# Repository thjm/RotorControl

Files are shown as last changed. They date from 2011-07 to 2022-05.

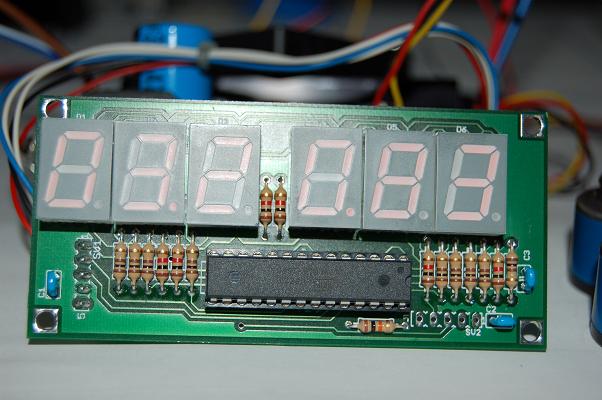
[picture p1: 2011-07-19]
DisplayUR/Doc/Display.jpg

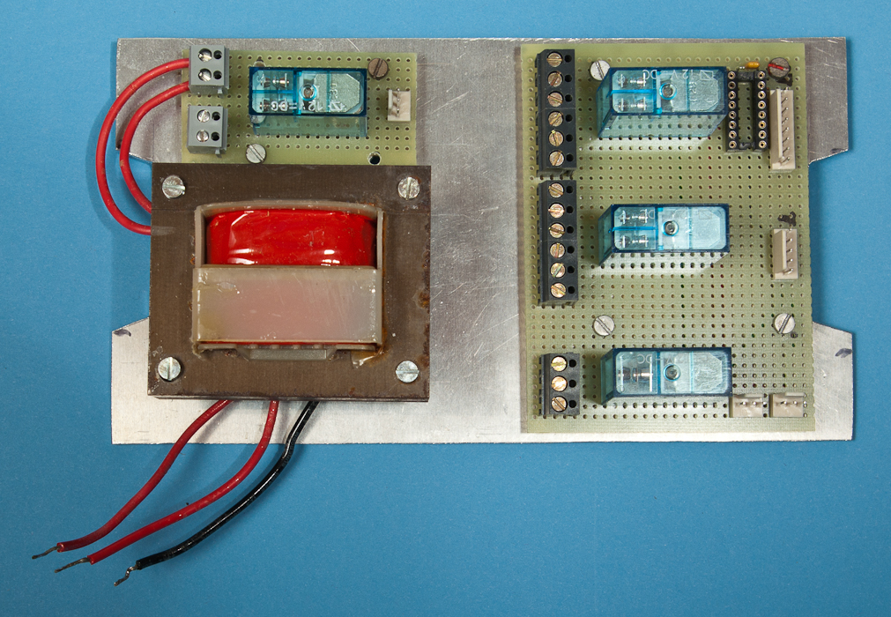
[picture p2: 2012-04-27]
Docu/RelayMountingPlate.jpg

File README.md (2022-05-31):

# About

RotorController is for controlling a simple antenna rotator using directionaly
signals from a 3D magnet sensor (and from a 3D accelerometer).

The software is split onto several micro controllers from Atmel's AVR family.

- the software for the display board (hardware design based on ATmega8 from U.Radig)
  is located in the directory ./DisplayUR
- the software for the ATmega8 at the remote magnetic/accelerometric sensor is
  located in the directory ./LSM303
- the software foreseen to run on the main ATmega32 is in the ./ directory
- further we have the Eagle circuit drawing of the various boards (my boards are
  all done on prototype boards, thus the eagle design was never verified):
  - AntennaBoard.sch : board with the mag./acc. sensor attached
    to the boom of the antenna
  - ButtonBoard.sch : board to hold push buttons and LEDs for the front panel
  - CPUBoard.sch : the board with the main CPU and connectors to the other
    board with a micro controller on them
  - PowerSupply.sch : main power supply, +12V and +5V
  - RelayBoard1.sch : board which holds relays for the direction and the release
    of the rotor brake (if available)
  - RelayBoard2.sch : supplement relay board, switches extra 22V AC for the
    used rotor type

## Directories

- Bootloader : contains the boot loader for the antenna sensor uC (not yet used?)

- Docu : various documentation files

- DisplayUR : parts takes from Ulrich Radig's (http://www.ulrichradig.de)
          PowerSupply project. The display unit presented there seems to be
          quite usable for a simple display here, just software needs to be
          adopted.

- Eagle : contains drawings and schemes done with the Eagle layout program

- Linux : various test programs, to be run on Linux

- LSM303 : library and example for the Pololu LSM303DLH 6-axis sensor
          breakout board. The boards contains a 3-axis magnetometer and a
          3-axis accelerometer.
          See also:
  - http://www.lipoly.de/index.php?main_page=product_info&products_id=165628
  - data sheet LSM303DLH.pdf
  - LSM303DLH-compass-app-note.pdf
  - LSM303DLH-orangutan-example-cde.zip
  - UM10204.pdf (I2C-bus specification)
  - https://github.com/ryantm/LSM303DLH (Arduino library)

- Sketches : Arduino sketches collection

- Test : directory containing various test programs for the 'rotorcontrol'
         hardware environment

## Requirements

- you need a cross-build environment for AVR micro controllers.
- the UART library from Peter Fleury, unpacked to a local directory
- the TWI master library from Peter Fleury, unpacked to a local directory
- the environment variable FLEURYHOME must point to the root of both directories

## Usage

Compile the software in the 3 directories ./LSM303, ./DIsplayUR and ./ by
typing make in ./ We have then:

- ./LSM303/lsm303read.hex : the software for the mag./acc. controller
- ./DisplayUR/i2cdisplay.hex : the software for the I2C controlled LED display
- ./rotorcontrol.hex : the software for the main processor

## Project Details

### Revision 1.1

- the display of UR's PS1 project will be used to display the current and the
  set value for the azimuth (directory DisplayUR)

- a LSM303DLH accelerometer and compass module will be used to determine the
  antenna direction. It will be coupled to the main electronics via a serial
  interface (coupled via RS-485)

- the main electronics module has the task to
  - receive direction information from the LSM303DLH
  - calculate/average the direction information and send it to the display
    module
  - compare the current direction with the preset value and pass this
    information to the rotator controller (software module)
  - switch the rotator motor in an appropriate way to achieve the desired
    direction; handle (optional) end-switches and a clutch/brake
  - get users input via push buttons (attached to the main electronics or to
    the display module?)
  - ...

### Revision 2.x

Managed somehow to destroy the antenna sensor during comissioning. As sensor is no
longer available, purchased successor LSM303DLHC (GY-511).

## References

- http://homepage.hispeed.ch/peterfleury/doxygen/avr-gcc-libraries/group__pfleury__uart.html, UART library
- http://homepage.hispeed.ch/peterfleury/doxygen/avr-gcc-libraries/group__pfleury__ic2master.html, TWI library
- https://github.com/ryantm/LSM303DLH, Arduini library for LSM303 like sensors

- https://pre-commit.com/

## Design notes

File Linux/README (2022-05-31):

$Id: README,v 1.2 2012/06/06 16:07:17 mathes Exp $

README file for Projekte/RotorControl/Linux
-----------------------------------------------------------------------------

This is the README file for the Linux (host) based test software (algorithms,
verification, etc.) of the rotator controller project.

analyzedat.cc - reads a file containing logged NMEA strings ($ACRAW sentences)
           acquired by the lsm303read.c program. The data are analyzed in two
	   passes:

	   1st pass: minimum and maximum values are determined
	   2nd pass: the magnetic (3D) heading of the acquired data is
	             calculated

	   The 3D heading is calculated using the MAG and ACC sensor readings.

compass1.cc - interactive version of the above program. This programs reads
           the NMEA strings from a serial interface which has to be specified
	   at the command line.

	   Different operation modes are possible:
	   c - calibration = acquiring data for new MAG min/max values
	   m - measure
	   d - debug output

*.dat - various data files from online

=============================================================================

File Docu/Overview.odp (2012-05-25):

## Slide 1

Relay 1

Rotator

2*22V

220V AC

Relay 4

Relay 2

@ antenna

LSM303

ATmega8

Relay 3

ULN2003

MAX485

220V AC

220V AC

12V-/5V-

0 0 0 1 2 3

MAX485

ATmega32

Buttons (5)

& LEDS (4)

MAX232

RS-232

Revision 1.1

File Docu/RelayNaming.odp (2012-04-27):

## Relay boards: naming scheme

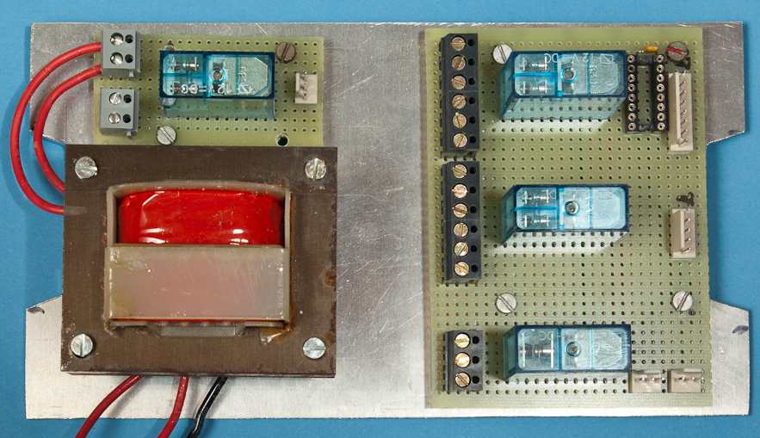
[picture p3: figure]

P1

S1

P1

S1

Relay K1

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
Relay K2

S2

O2

O1

S1

Relay K3

P1

## Relay boards: cabling scheme

P1

S1

P1

S1

Relay K1

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
Relay K2

S2

O2

O1

S1

Relay K3

P1

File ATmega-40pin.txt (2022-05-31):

$Id: ATmega-40pin.txt,v 1.1 2012/04/11 21:29:31 mathes Exp $

Pinouts for 40 pin ATmega uController
------------------------------------------------------------------------------

       16/32             644                  644A/644PA/1284/1284P
---------------------------------------------------------------------
  1  PB0 (XCK/T0)       (PCINT8/XCK0/T0)      (PCINT8/XCK0/T0)
  2  PB1 (T1)           (PCINT9/CLK0/T1)      (PCINT9/CLK0/T1)
  3  PB2 (INT2/AIN0)    (PCINT10/INT2/AIN0)   (PCINT10/INT2/AIN0)
  4  PB3 (OC0/AIN1)     (PCINT11/OC0A/AIN1)   (PCINT11/OC0A/AIN1)
  5  PB4 (!SS)          (PCINT12/OC0B/!SS)    (PCINT12/OC0B/!SS)
  6  PB5 (MOSI)         (PCINT13/MOSI)        (PCINT13/MOSI)
  7  PB6 (MISO)         (PCINT14/MISO)        (PCINT14/MISO)
  8  PB7 (SCK)          (PCINT15/SCK)         (PCINT15/SCK)
  9  !RESET
 10  VCC

 11  GND
 12  XTAL2
 13  XTAL1
 14  PD0 (RXD)          (PCINT24/RXD0)        (PCINT24/RXD0)
 15  PD1 (TXD)          (PCINT25/TXD0)        (PCINT25/TXD0)
 16  PD2 (INT0)         (PCINT26/INT0)        (PCINT26/RXD1/INT0)
 17  PD3 (INT1)         (PCINT27/INT1)        (PCINT27/TXD1/INT1)
 18  PD4 (OC1B)         (PCINT28/OC1B)        (PCINT28/XCK1/OC1B)
 19  PD5 (OC1A)         (PCINT29/OC1A)        (PCINT29/OC1A)
 20  PD6 (ICP1)         (PCINT30/OC2B/ICP1)   (PCINT30/OC2B/ICP1)

 21  PD7 (OC2)          (PCINT31/OC2A)
 22  PC0 (SCL)          (PCINT16/SCL)         (PCINT16/SCL)
 23  PC1 (SDA)          (PCINT17/SDA)         (PCINT17/SDA)
 24  PC2 (TCK)          (PCINT18/TCK)         (PCINT18/TCK)
 25  PC3 (TMS)          (PCINT19/TMS)         (PCINT19/TMS)
 26  PC4 (TDO)          (PCINT20/TDO)         (PCINT20/TDO)
 27  PC5 (TDI)          (PCINT21/TDI)         (PCINT21/TDI)
 28  PC6 (TOSC1)        (PCINT22/TOSC1)       (PCINT22/TOSC1)
 29  PC7 (TOSC2)        (PCINT23/TOSC2)       (PCINT23/TOSC2)
 30  AVCC

 31  GND
 32  AREF
 33  PA7 (ADC7)         (PCINT7/ADC7)         (PCINT7/ADC7)
 34  PA6 (ADC6)         (PCINT6/ADC6)         (PCINT6/ADC6)
 35  PA5 (ADC5)         (PCINT5/ADC5)         (PCINT5/ADC5)
 36  PA4 (ADC4)         (PCINT4/ADC4)         (PCINT4/ADC4)
 37  PA3 (ADC3)         (PCINT3/ADC3)         (PCINT3/ADC3)
 38  PA2 (ADC2)         (PCINT2/ADC2)         (PCINT2/ADC2)
 39  PA1 (ADC1)         (PCINT1/ADC1)         (PCINT1/ADC1)
 40  PA0 (ADC0)         (PCINT0/ADC0)         (PCINT0/ADC0)
==============================================================================

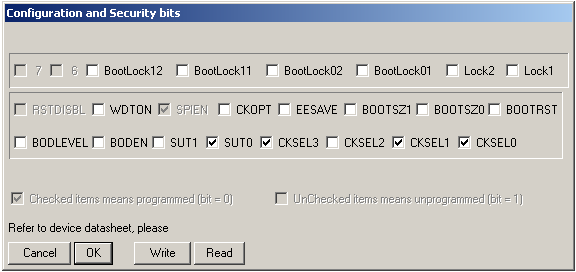
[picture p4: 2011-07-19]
DisplayUR/Doc/ATmega8_FuseBits.png

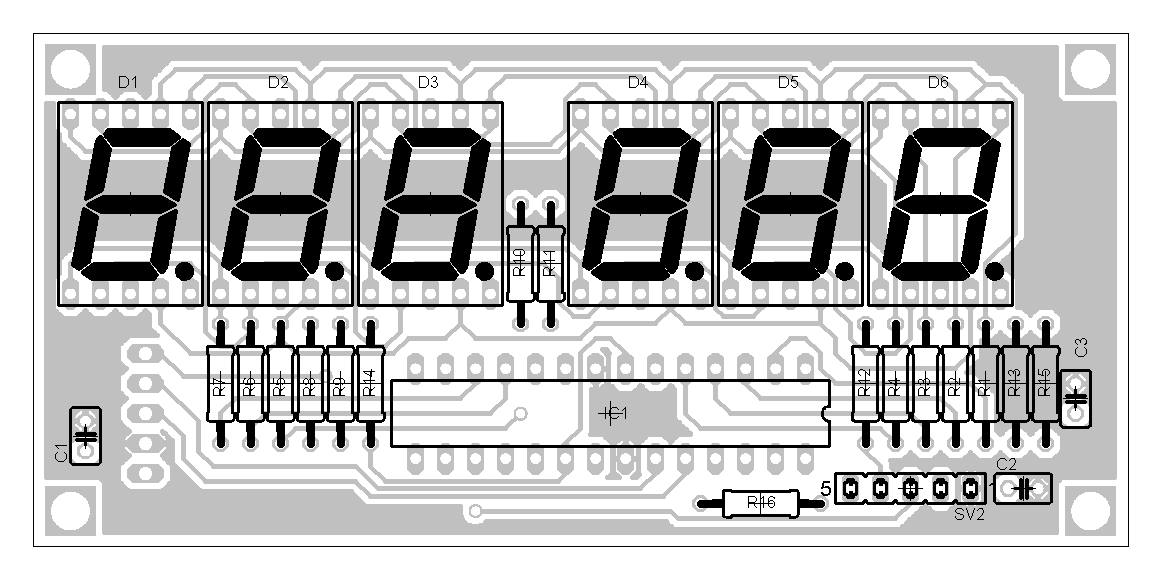
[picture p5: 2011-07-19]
DisplayUR/Doc/Display_Top.png

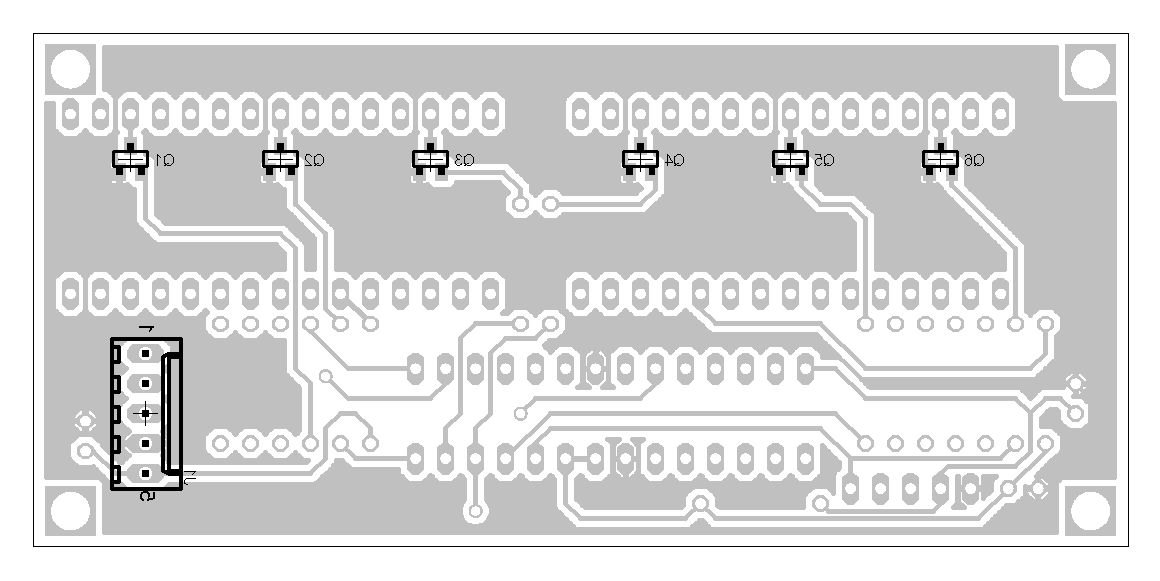
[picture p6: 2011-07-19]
DisplayUR/Doc/Display_Bot.png

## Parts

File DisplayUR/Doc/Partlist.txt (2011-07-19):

Partlist

Part     		Bestellnr. Reichelt
C1..C3       		Z5U-2,5 100N
D1..D6                  SC 52-11 GN (7 Segmentanzeige grün)
IC1			ATMEGA 8-16 DIP
J1			PSS 254/5G
Q1..Q6       		BC847
R1..R7, R14, R15	1/4W 120
R8..R13      		1/4W 1k
R16			1/4W 10k

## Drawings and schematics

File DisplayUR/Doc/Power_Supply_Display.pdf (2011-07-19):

Spannung | Strom

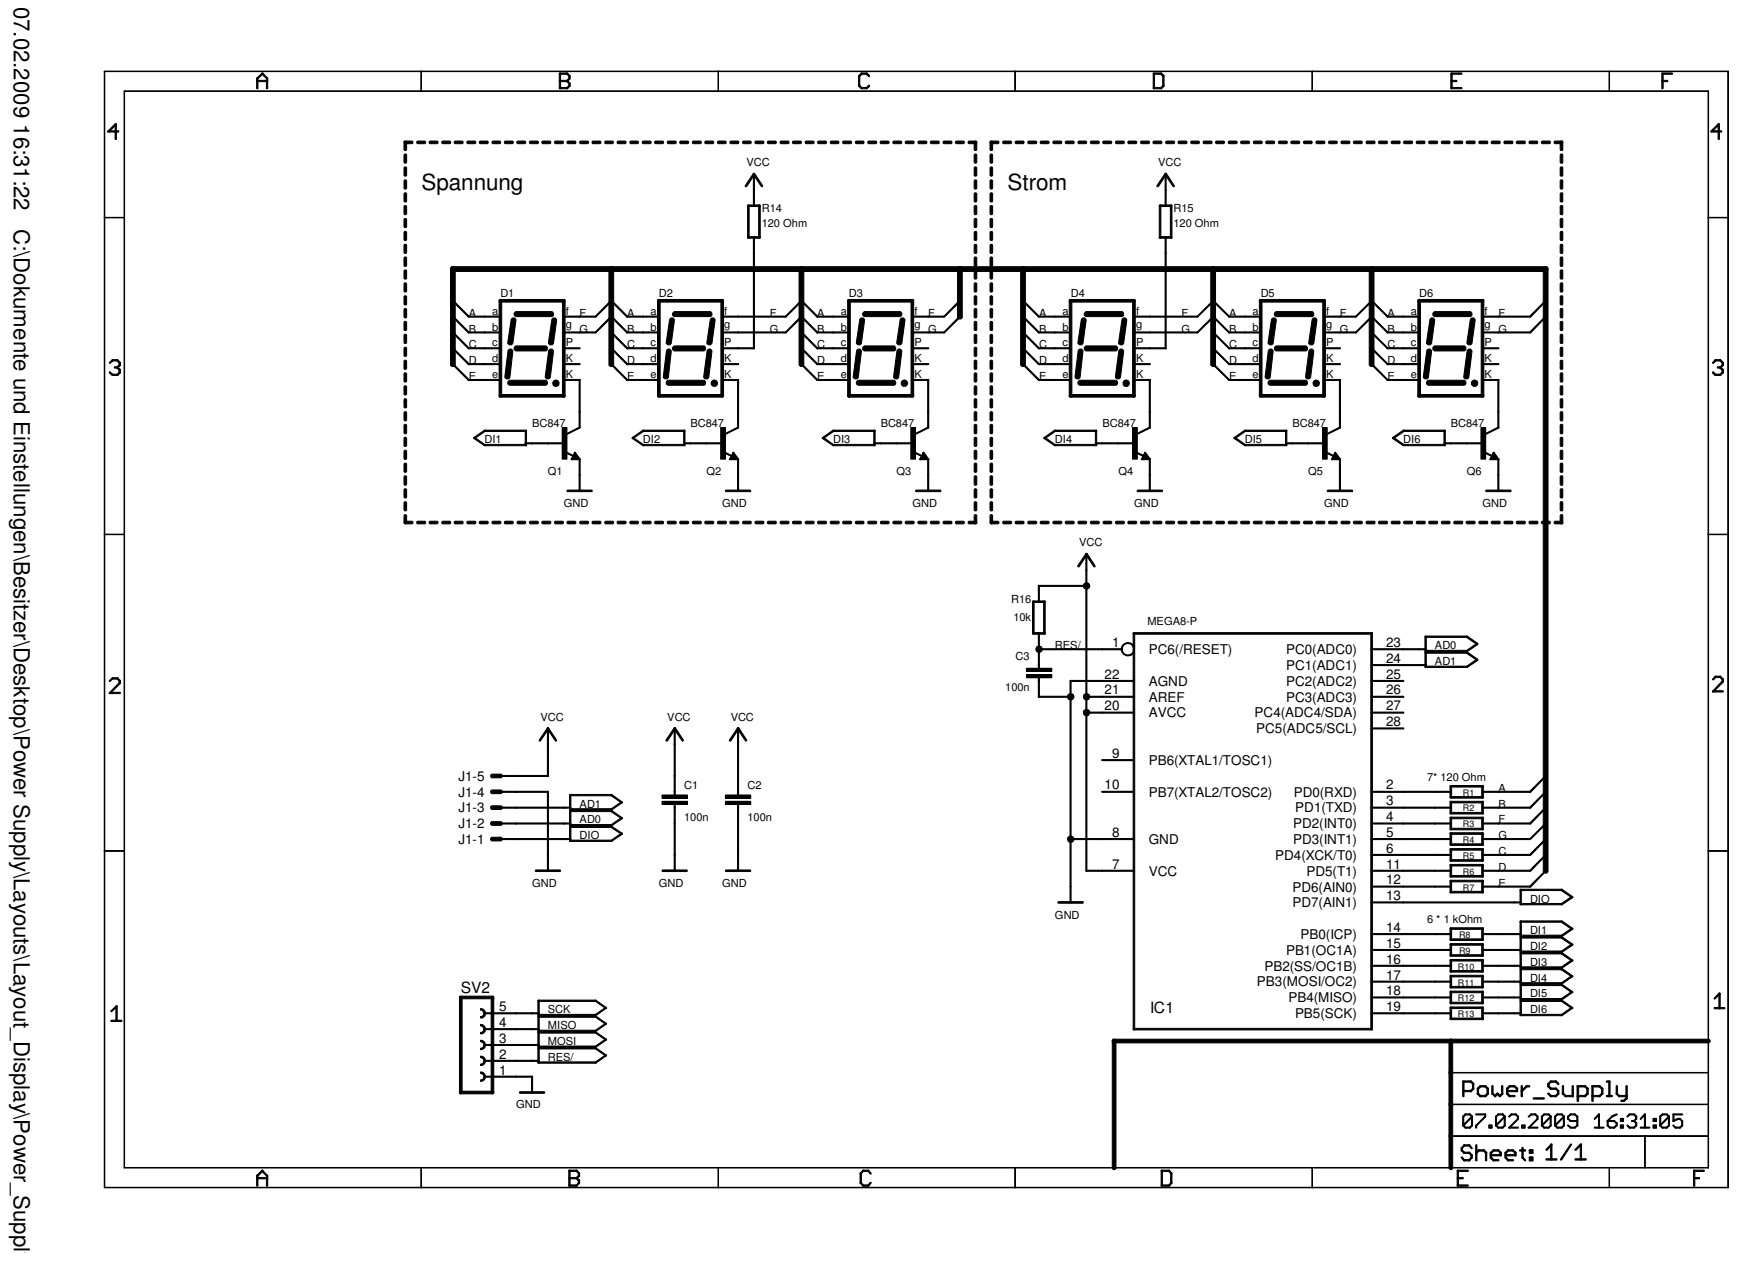
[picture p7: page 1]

07.02.2009 16:31:22 C:\Dokumente und Einstellungen\Besitzer\Desktop\Power Supply\Layouts\Layout_Display\Power_Supply

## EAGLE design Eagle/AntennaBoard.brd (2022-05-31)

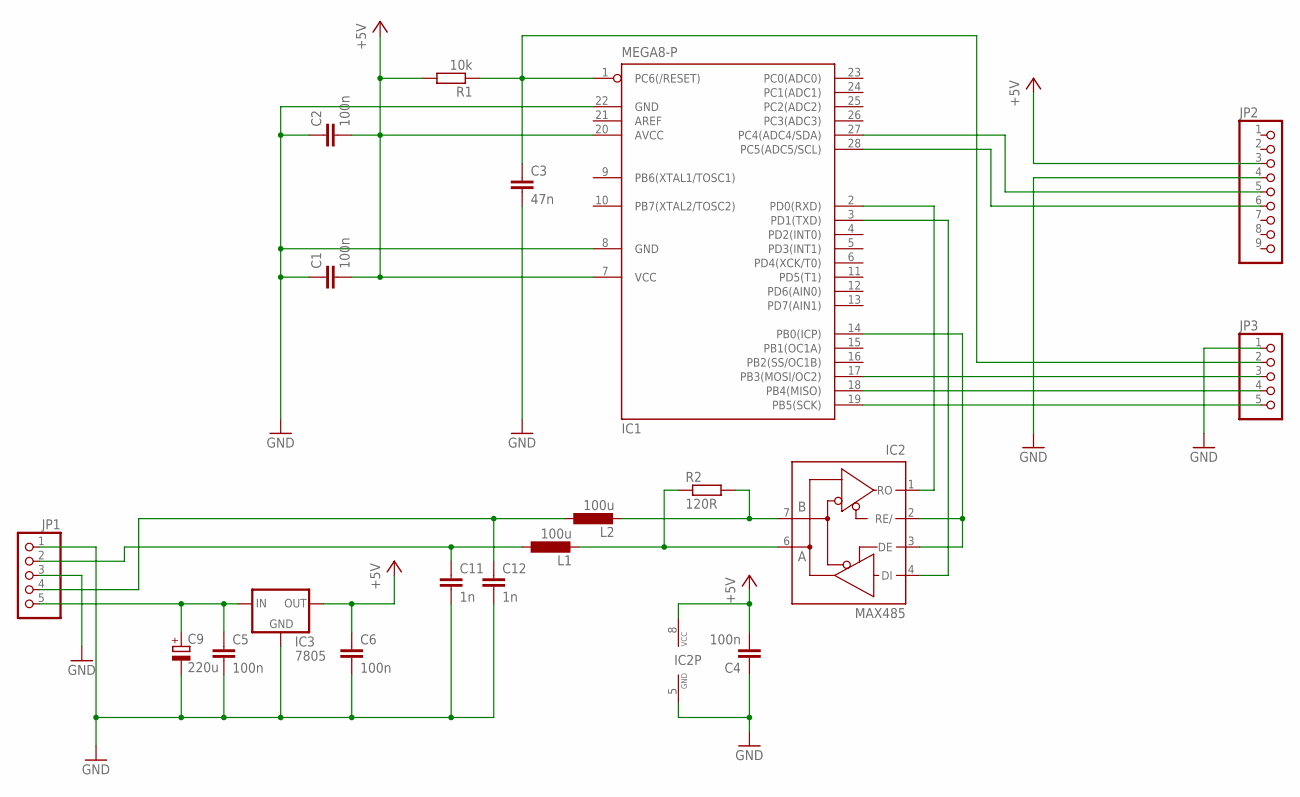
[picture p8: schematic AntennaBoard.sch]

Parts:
C1, C2, C4, C5, C6: 100n; C050-024X044
C3: 47n; C050-024X044
C9: 220u; E5-10,5
C11, C12: 1n; C025-024X044
IC1: MEGA8-P; DIL28-3
IC2: MAX485; DIL08
IC3: 7805; 78XXL
JP1: PINHD-1X5/90; 1X05/90
JP2: PINHD-1X9; 1X09
JP3: PINHD-1X5; 1X05
L1, L2: 100u; 0207/12
R1: 10k; 0207/10
R2: 120R; 0207/10

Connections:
+5V: C1.2, C2.2, C4.2, C6.1, IC1.7 (VCC), IC1.20 (AVCC), IC2.8 (VCC), IC3.OUT, JP2.3, R1.2
GND: C1.1, C2.1, C3.2, C4.1, C5.2, C6.2, C9.-, C11.2, C12.2, IC1.8 (GND), IC1.22 (GND), IC2.5 (GND), IC3.GND, JP1.1, JP1.3, JP2.4, JP3.1
unnamed: C5.1, C9.+, IC3.IN, JP1.5
unnamed: IC2.6 (A), L1.2, R2.1
unnamed: C12.1, JP1.4, L2.1
unnamed: IC1.28 (PC5(ADC5/SCL)), JP2.6
unnamed: C3.1, IC1.1 (PC6(/RESET)), JP3.2, R1.1
unnamed: IC1.27 (PC4(ADC4/SDA)), JP2.5
unnamed: IC1.14 (PB0(ICP)), IC2.2 (RE/), IC2.3 (DE)
unnamed: IC1.2 (PD0(RXD)), IC2.1 (RO)
unnamed: IC1.3 (PD1(TXD)), IC2.4 (DI)
unnamed: IC2.7 (B), L2.2, R2.2
unnamed: C11.1, JP1.2, L1.1
unnamed: IC1.17 (PB3(MOSI/OC2)), JP3.3
unnamed: IC1.18 (PB4(MISO)), JP3.4
unnamed: IC1.19 (PB5(SCK)), JP3.5

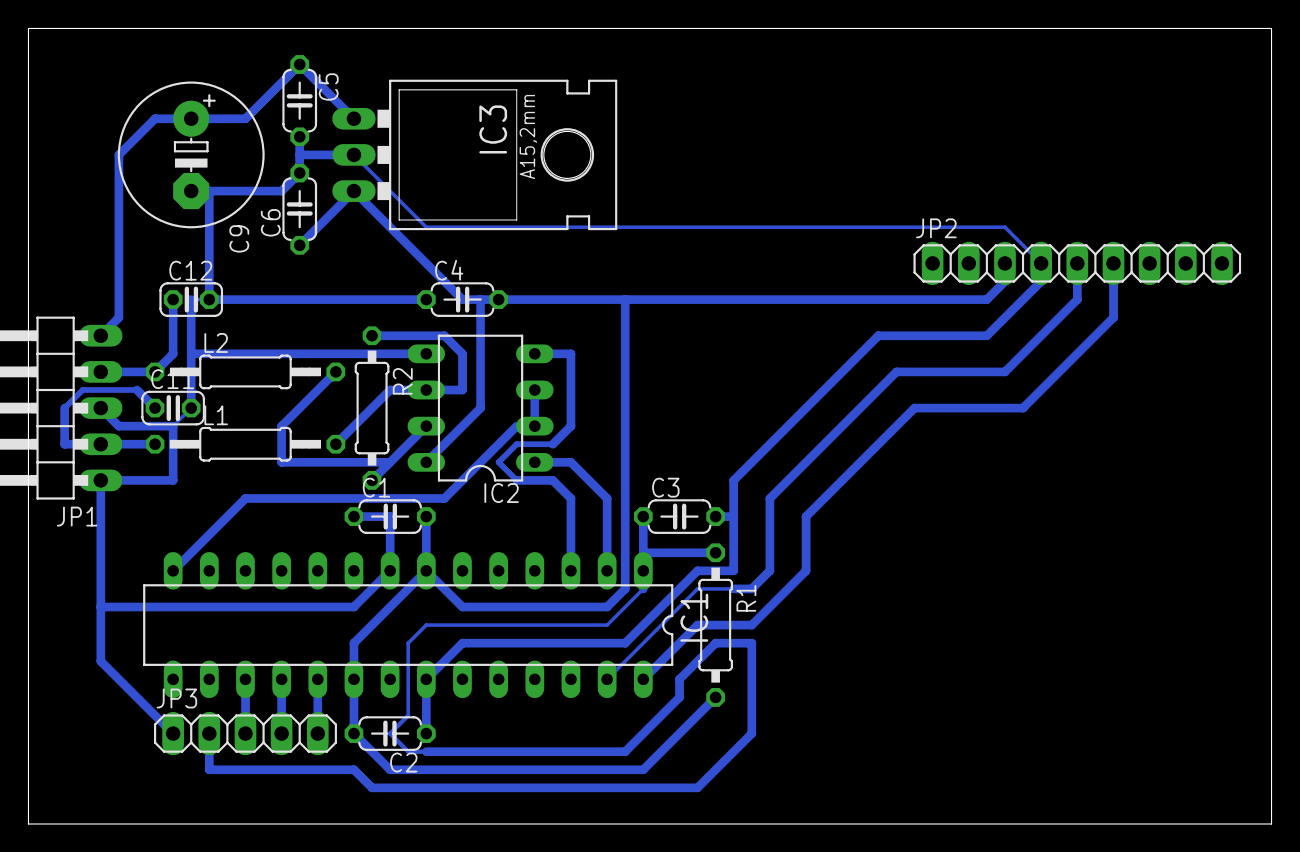
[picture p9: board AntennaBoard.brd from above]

Board: 2 copper layers, 87.3 x 55.9 mm, 19 parts (0 on the bottom side), 16 nets.

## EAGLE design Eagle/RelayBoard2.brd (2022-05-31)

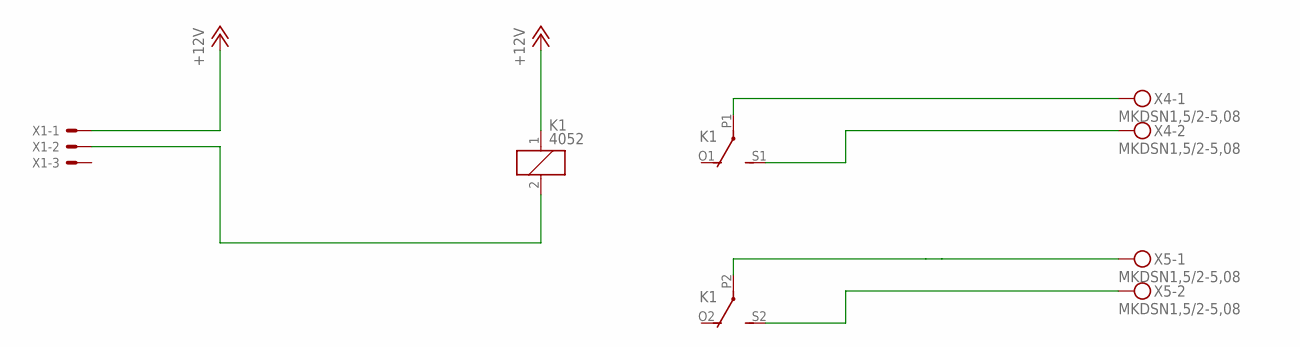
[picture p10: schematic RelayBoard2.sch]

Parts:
K1: 4052; F4052
X1: KK-156-3
X4, X5: MKDSN1,5/2-5,08

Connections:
+12V: K1.1, X1.1
unnamed: K1.2, X1.2
unnamed: K1.P2, X5.1
unnamed: K1.S2 (S), X5.2
unnamed: K1.S1 (S), X4.2
unnamed: K1.P1, X4.1

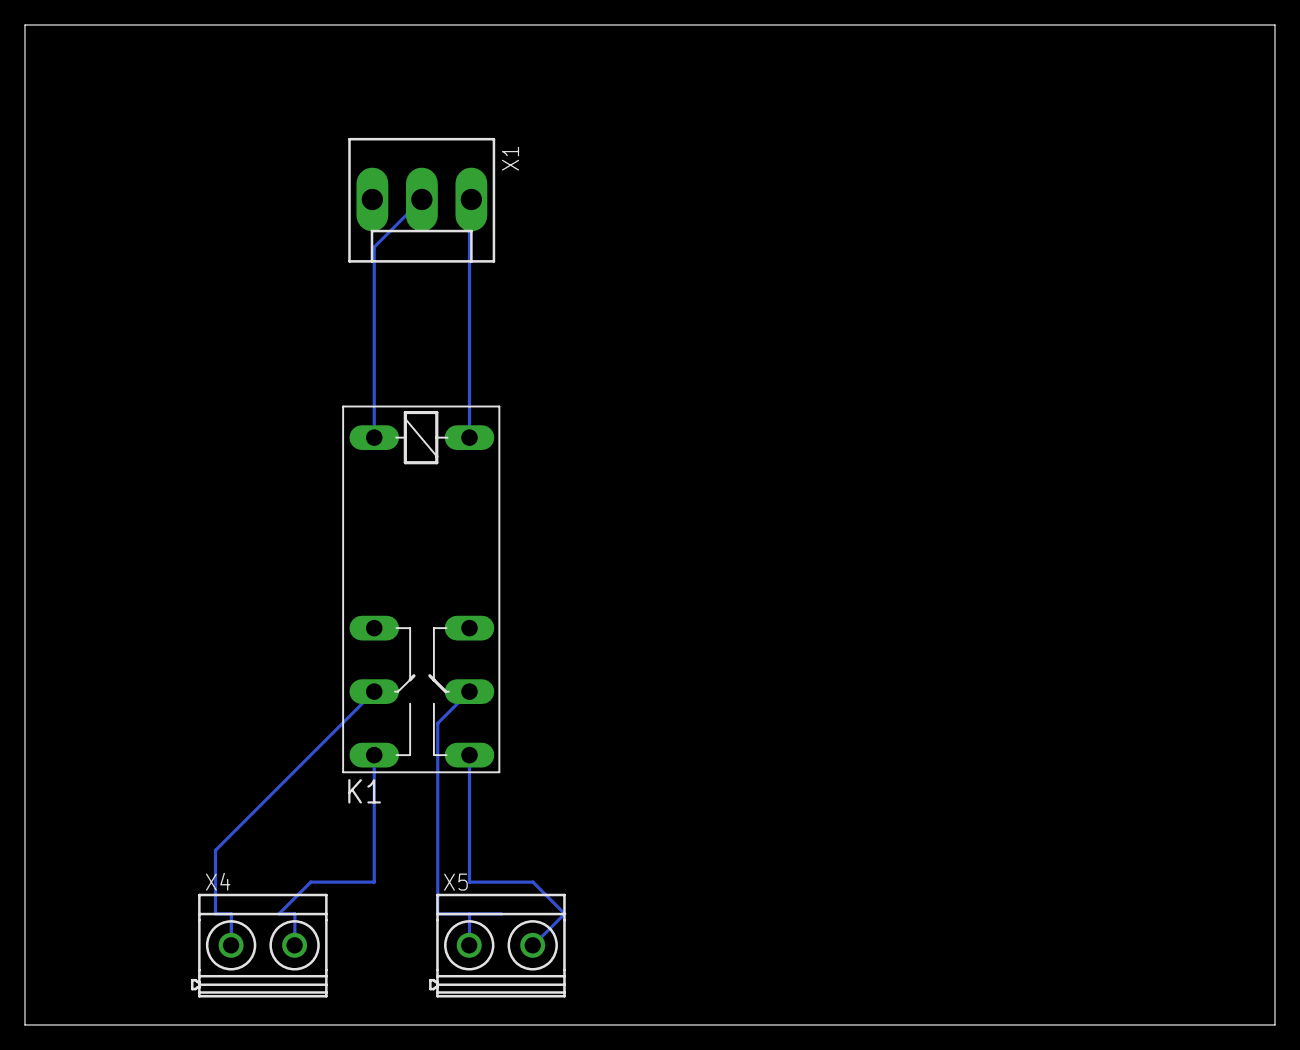
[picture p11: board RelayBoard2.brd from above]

Board: 2 copper layers, 100.0 x 80.0 mm, 4 parts (0 on the bottom side), 6 nets.

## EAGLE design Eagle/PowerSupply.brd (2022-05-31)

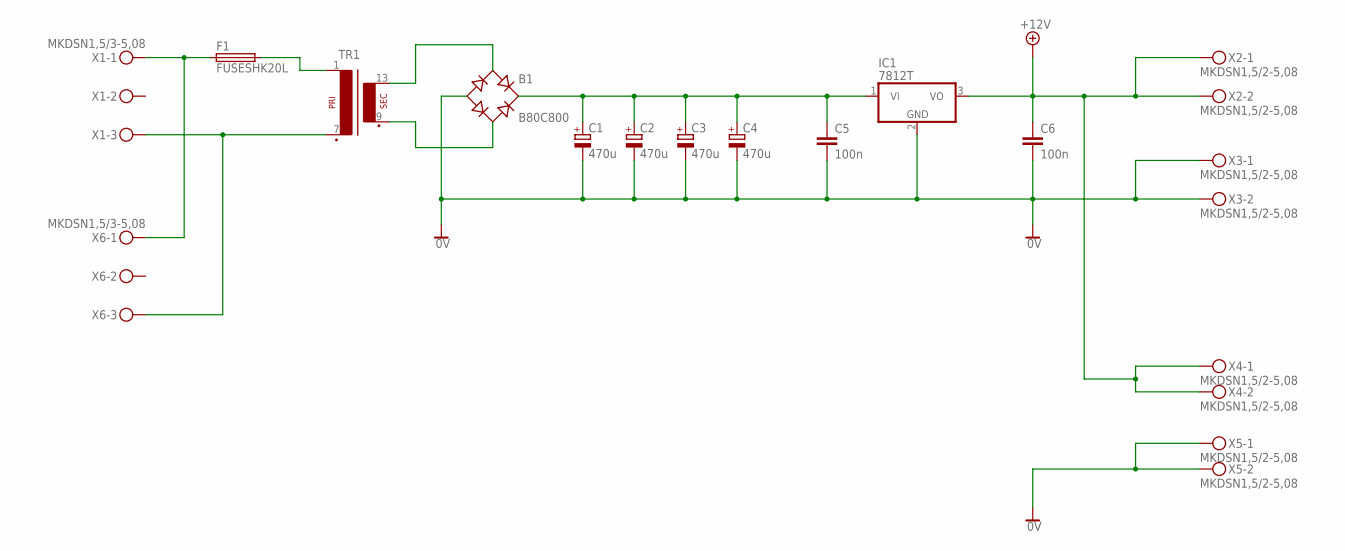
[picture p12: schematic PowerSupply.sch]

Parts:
B1: B80C800; B-DIL
C1, C2, C3, C4: 470u; E5-10,5
C5, C6: 100n; C050-024X044
F1: FUSESHK20L; SHK20L
IC1: 7812T; TO220H
TR1: EI54-1B
X1: MKDSN1,5/3-5,08
X2, X3, X4, X5: MKDSN1,5/2-5,08
X6: MKDSN1,5/3-5,08; MPN SMKDSN1,5/3-5,08

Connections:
0V: B1.-, C1.-, C2.-, C3.-, C4.-, C5.2, C6.2, IC1.2 (GND), X3.1, X3.2, X5.1, X5.2
+12V: C6.1, IC1.3 (VO), X2.1, X2.2, X4.1, X4.2
unnamed: F1.1A (1), X1.1, X6.1
unnamed: F1.2A (2), TR1.1
unnamed: B1.AC1, TR1.13 (S4)
unnamed: B1.AC2, TR1.9 (S3)
unnamed: B1.+, C1.+, C2.+, C3.+, C4.+, C5.1, IC1.1 (VI)
unnamed: TR1.7 (P2), X1.3, X6.3

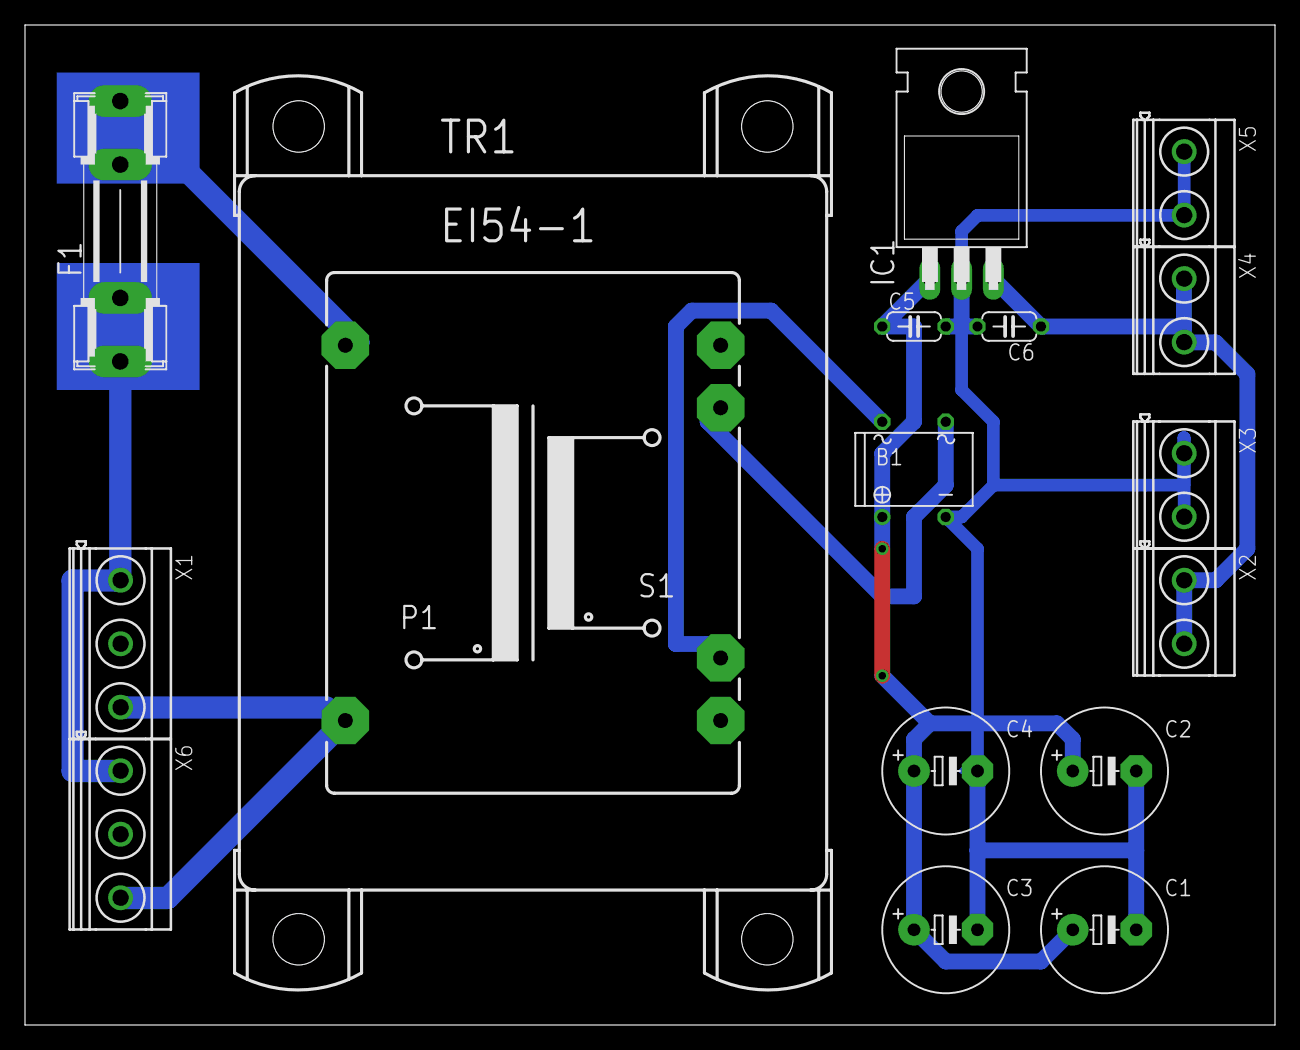
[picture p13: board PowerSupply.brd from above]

Board: 2 copper layers, 100.0 x 80.0 mm, 16 parts (0 on the bottom side), 8 nets.

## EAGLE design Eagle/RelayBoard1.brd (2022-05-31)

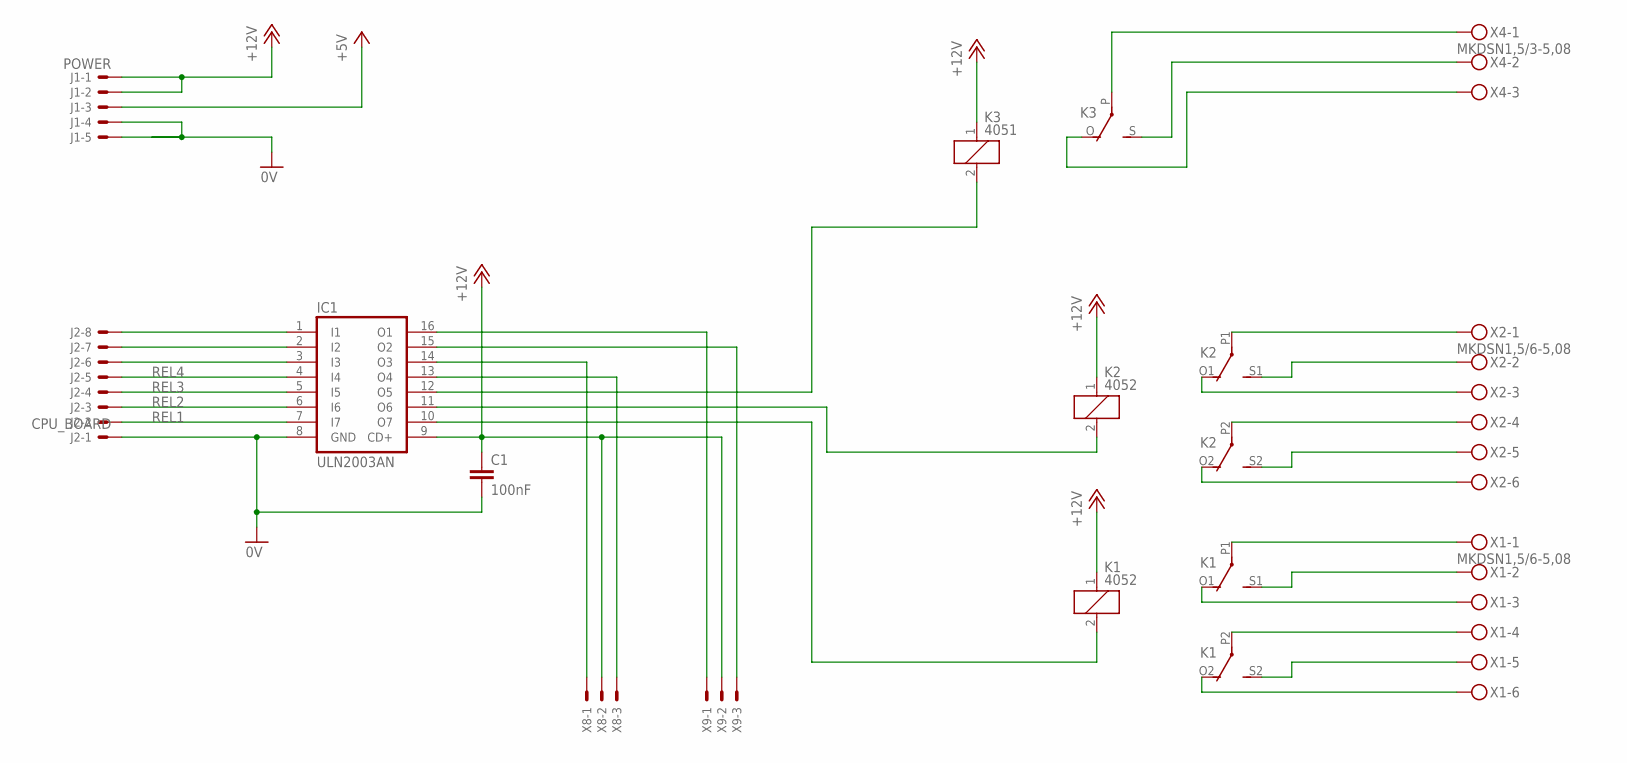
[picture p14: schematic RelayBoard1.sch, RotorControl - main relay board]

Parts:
C1: 100nF; C025-025X050
IC1: ULN2003AN; DIL16
J1: POWER; 6410-05
J2: CPU_BOARD; 6410-08
K1, K2: 4052; F4052
K3: 4051; G2R
X1, X2: MKDSN1,5/6-5,08
X4: MKDSN1,5/3-5,08; MPN SMKDSN1,5/3-5,08
X8, X9: KK-156-3

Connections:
0V: C1.2, IC1.8 (GND), J1.4, J1.5, J2.1
+5V: J1.3
+12V: C1.1, IC1.9 (CD+), J1.1, J1.2, K1.1, K2.1, K3.1, X8.2, X9.2
unnamed: K3.P, X4.1
unnamed: K3.S, X4.2
unnamed: K3.O, X4.3
unnamed: IC1.10 (O7), K1.2
unnamed: K2.P1, X2.1
unnamed: K2.S1 (S), X2.2
unnamed: K2.O1 (O), X2.3
unnamed: K2.P2, X2.4
unnamed: K2.S2 (S), X2.5
unnamed: K2.O2 (O), X2.6
unnamed: K1.P1, X1.1
unnamed: K1.S1 (S), X1.2
unnamed: K1.O1 (O), X1.3
unnamed: K1.P2, X1.4
unnamed: K1.S2 (S), X1.5
unnamed: K1.O2 (O), X1.6
unnamed: IC1.3 (I3), J2.6
unnamed: IC1.2 (I2), J2.7
unnamed: IC1.1 (I1), J2.8
unnamed: IC1.11 (O6), K2.2
unnamed: IC1.12 (O5), K3.2
unnamed: IC1.14 (O3), X8.1
unnamed: IC1.13 (O4), X8.3
unnamed: IC1.16 (O1), X9.1
unnamed: IC1.15 (O2), X9.3
REL1: IC1.7 (I7), J2.2
REL2: IC1.6 (I6), J2.3
REL3: IC1.5 (I5), J2.4
REL4: IC1.4 (I4), J2.5

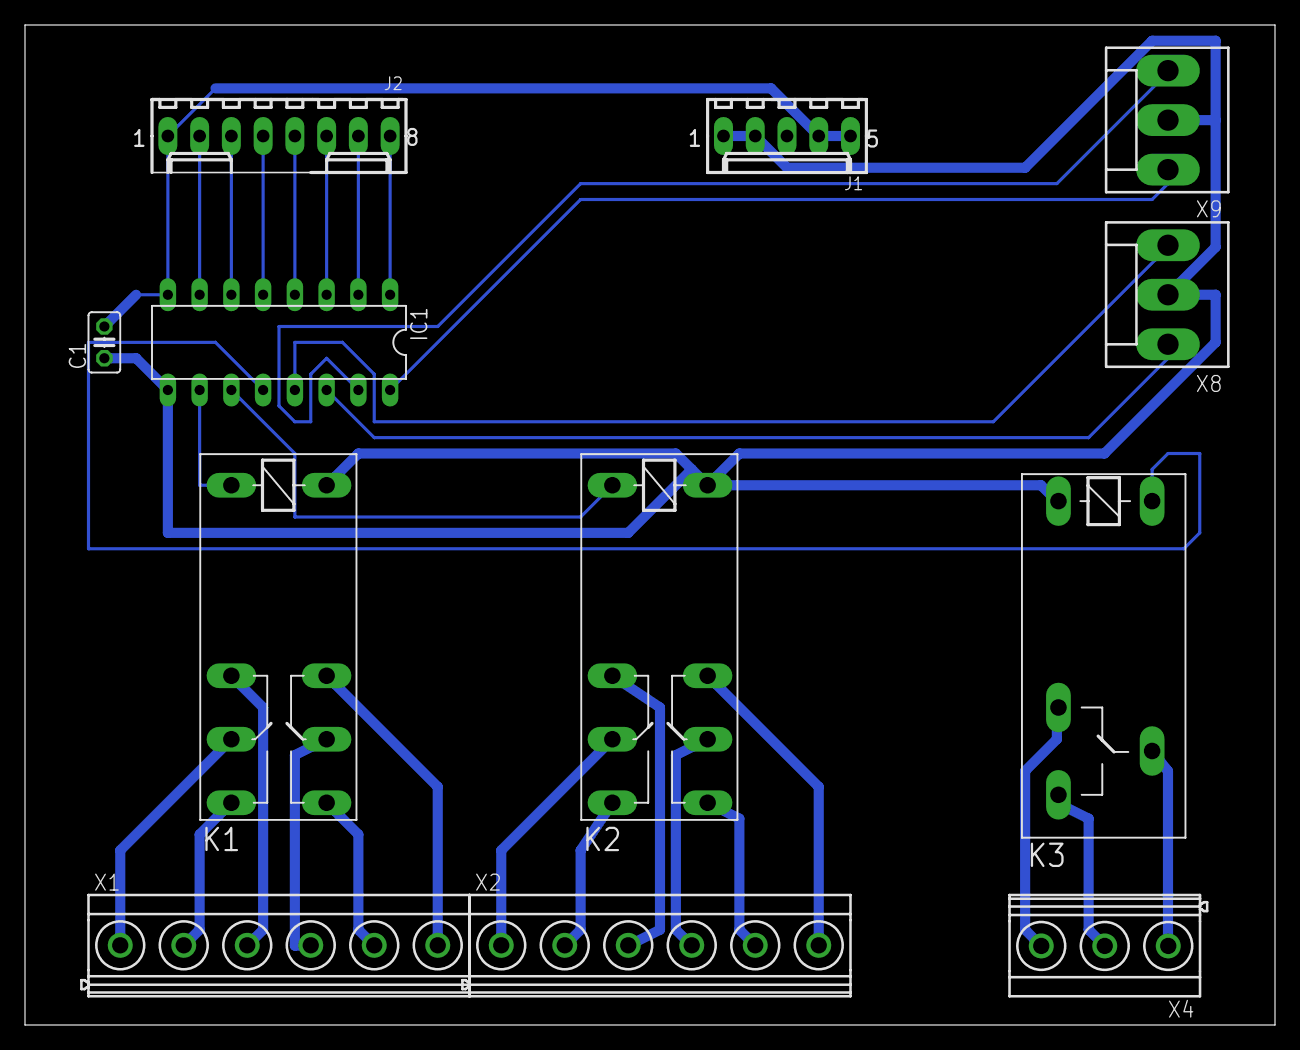
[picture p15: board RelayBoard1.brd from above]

Board: 2 copper layers, 100.0 x 80.0 mm, 12 parts (0 on the bottom side), 31 nets.

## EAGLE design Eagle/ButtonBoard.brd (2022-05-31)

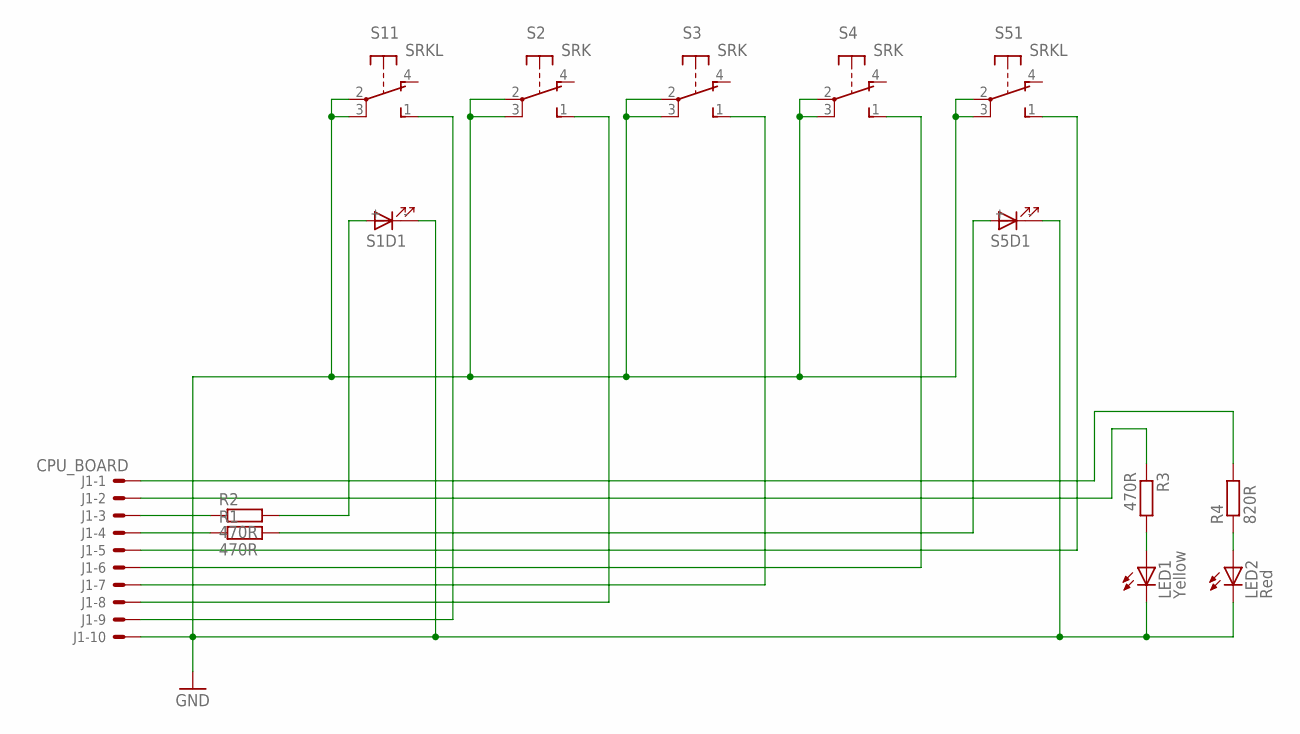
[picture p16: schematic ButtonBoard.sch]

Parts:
J1: CPU_BOARD; 7395-10
LED1: Yellow; LED3MM
LED2: Red; LED3MM
R1, R2, R3: 470R; 0207/10
R4: 820R; 0207/10
S1, S5: SRKL
S2, S3, S4: SRK

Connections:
GND: J1.10, LED1.K (C), LED2.K (C), S1.2, S1.3, S1.- (C), S2.2, S2.3, S3.2, S3.3, S4.2, S4.3, S5.2, S5.3, S5.- (C)
unnamed: R2.2, S1.+ (A)
unnamed: J1.3, R2.1
unnamed: J1.4, R1.1
unnamed: J1.9, S1.1 (S)
unnamed: R1.2, S5.+ (A)
unnamed: J1.8, S2.1 (S)
unnamed: J1.7, S3.1 (S)
unnamed: J1.6, S4.1 (S)
unnamed: J1.5, S5.1 (S)
unnamed: LED2.A, R4.1
unnamed: LED1.A, R3.2
unnamed: J1.2, R3.1
unnamed: J1.1, R4.2

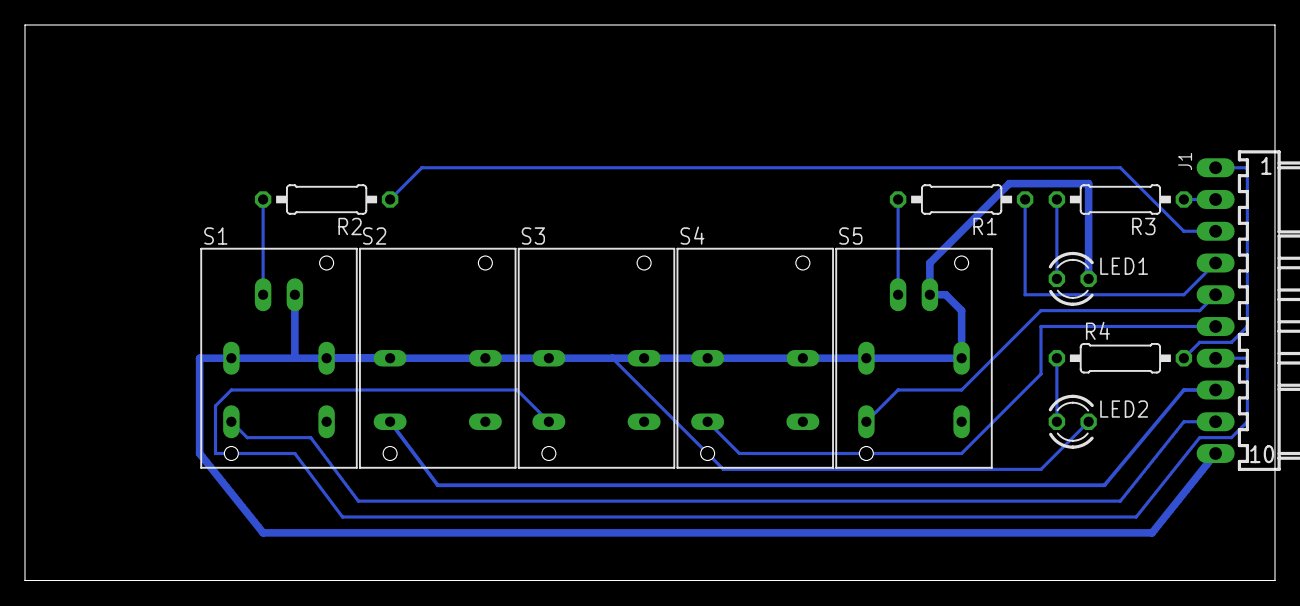
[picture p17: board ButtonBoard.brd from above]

Board: 2 copper layers, 100.0 x 44.4 mm, 12 parts (0 on the bottom side), 14 nets.

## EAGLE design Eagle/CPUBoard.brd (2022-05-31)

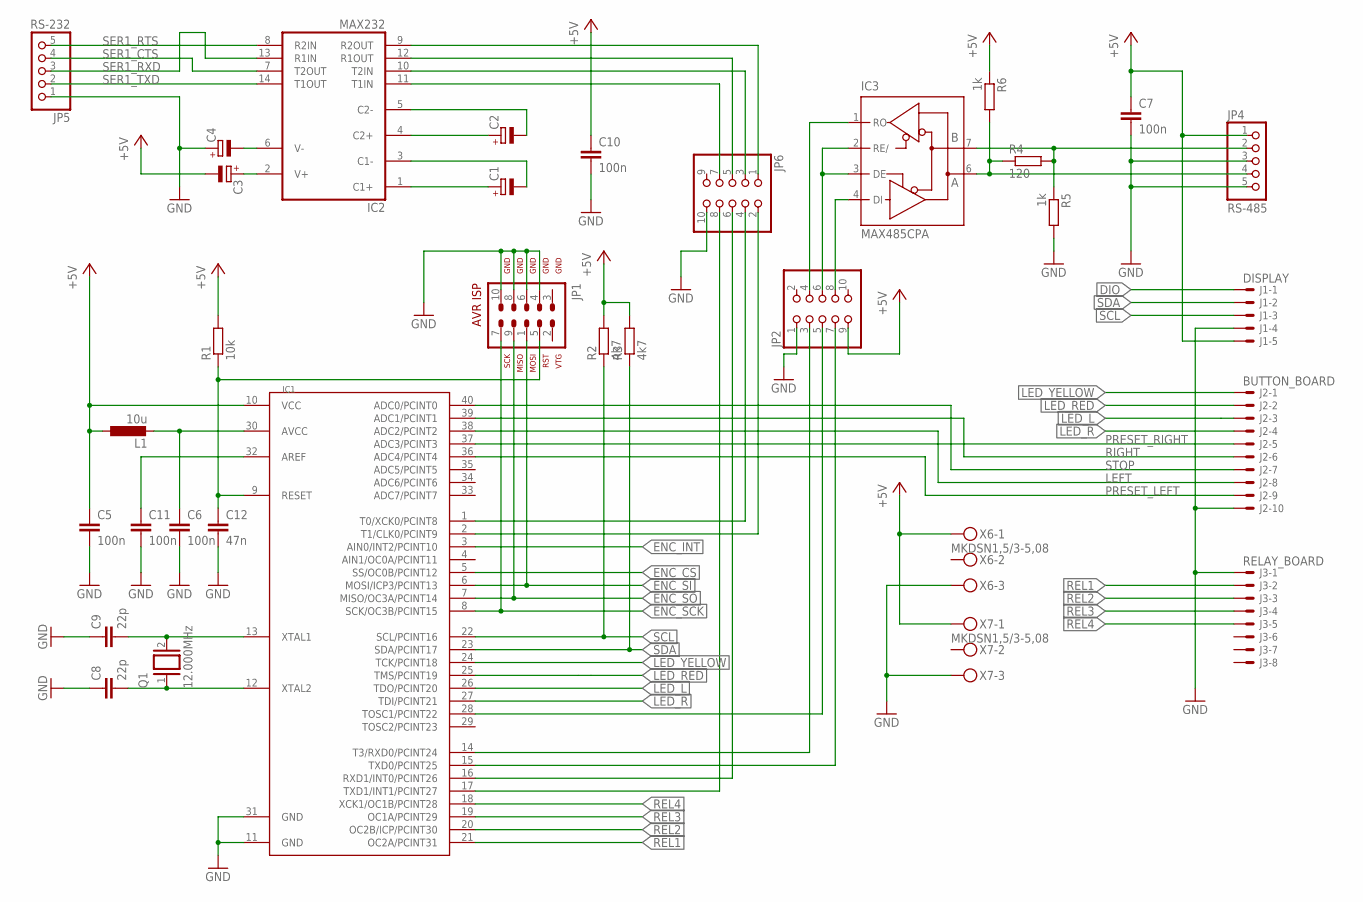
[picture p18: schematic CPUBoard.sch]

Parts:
C1, C2, C3, C4: CPOL-EUE2,5-6E; E2,5-6E
C5, C6, C7, C10, C11: 100n; C025-025X050
C8, C9: 22p; C025-024X044
C12: 47n; C025-025X050
IC1: MEGA1284P; DIL40
IC2: MAX232; DIL16
IC3: MAX485CPA; DIL08
J1: DISPLAY; 6410-05
J2: BUTTON_BOARD; 6410-10
J3: RELAY_BOARD; 6410-08
JP1: AVR-ISP-10
JP2, JP6: PINHD-2X5; 2X05
JP4: RS-485; 1X05
JP5: RS-232; 1X05
L1: 10u; 0207/10
Q1: 12.000MHz; QS
R1: 10k; 0207/10
R2, R3: 4k7; 0207/10
R4: 120; 0207/10
R5, R6: 1k; 0207/10
X6, X7: MKDSN1,5/3-5,08

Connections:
+5V: C3.-, C5.1, C7.1, C10.1, IC1.10 (VCC), J1.5, JP2.9, JP4.1, L1.1, R1.2, R2.2, R3.2, R6.1, X6.1, X7.1
DIO: J1.1
ENC_CS: IC1.5 (SS/OC0B/PCINT12)
ENC_INT: IC1.3 (AIN0/INT2/PCINT10)
ENC_SCK: IC1.8 (SCK/OC3B/PCINT15), JP1.7
ENC_SI: IC1.6 (MOSI/ICP3/PCINT13), JP1.1
ENC_SO: IC1.7 (MISO/OC3A/PCINT14), JP1.9
GND: C4.+, C5.2, C6.2, C7.2, C8.1, C9.1, C10.2, C11.2, C12.2, IC1.11 (GND), IC1.31 (GND), IC2.15 (GND), IC3.5 (GND), J1.4, J2.10, J3.1, JP1.4, JP1.6, JP1.8, JP1.10, JP2.1, JP4.3, JP4.5, JP5.1, JP6.10, R5.2, X6.3, X7.3
LED_L: IC1.26 (TDO/PCINT20), J2.3
LED_R: IC1.27 (TDI/PCINT21), J2.4
LED_RED: IC1.25 (TMS/PCINT19), J2.2
LED_YELLOW: IC1.24 (TCK/PCINT18), J2.1
LEFT: IC1.38 (ADC2/PCINT2), J2.8
unnamed: C9.2, IC1.13 (XTAL1), Q1.2
unnamed: C8.2, IC1.12 (XTAL2), Q1.1
unnamed: C12.1, IC1.9 (RESET), JP1.5, R1.1
unnamed: IC2.11 (T1IN), JP6.7
unnamed: C1.+, IC2.1 (C1+)
unnamed: C1.-, IC2.3 (C1-)
unnamed: C2.+, IC2.4 (C2+)
unnamed: C2.-, IC2.5 (C2-)
unnamed: C3.+, IC2.2 (V+)
unnamed: C4.-, IC2.6 (V-)
unnamed: IC2.12 (R1OUT), JP6.5
unnamed: C6.1, IC1.30 (AVCC), L1.2
unnamed: IC1.14 (T3/RXD0/PCINT24), JP2.3
unnamed: IC1.15 (TXD0/PCINT25), JP2.7
unnamed: IC1.28 (TOSC1/PCINT22), JP2.5
unnamed: IC1.1 (T0/XCK0/PCINT8), JP6.4
unnamed: IC3.6 (A), JP4.4, R4.1, R6.2
unnamed: IC3.7 (B), JP4.2, R4.2, R5.1
unnamed: C11.1, IC1.32 (AREF)
unnamed: IC3.2 (RE/), IC3.3 (DE), JP2.6
unnamed: IC3.4 (DI), JP2.8
unnamed: IC1.16 (RXD1/INT0/PCINT26), JP6.6
unnamed: IC3.1 (RO), JP2.4
unnamed: IC1.17 (TXD1/INT1/PCINT27), JP6.8
unnamed: IC1.2 (T1/CLK0/PCINT9), JP6.2
unnamed: IC2.9 (R2OUT), JP6.1
unnamed: IC2.10 (T2IN), JP6.3
PRESET_LEFT: IC1.36 (ADC4/PCINT4), J2.9
PRESET_RIGHT: IC1.37 (ADC3/PCINT3), J2.5
REL1: IC1.21 (OC2A/PCINT31), J3.2
REL2: IC1.20 (OC2B/ICP/PCINT30), J3.3
REL3: IC1.19 (OC1A/PCINT29), J3.4
REL4: IC1.18 (XCK1/OC1B/PCINT28), J3.5
RIGHT: IC1.39 (ADC1/PCINT1), J2.6
SCL: IC1.22 (SCL/PCINT16), J1.3, R2.1
SDA: IC1.23 (SDA/PCINT17), J1.2, R3.1
SER1_CTS: IC2.13 (R1IN), JP5.3
SER1_RTS: IC2.8 (R2IN), JP5.5
SER1_RXD: IC2.7 (T2OUT), JP5.4
SER1_TXD: IC2.14 (T1OUT), JP5.2
STOP: IC1.40 (ADC0/PCINT0), J2.7
VCC: IC2.16 (VCC), IC3.8 (VCC)

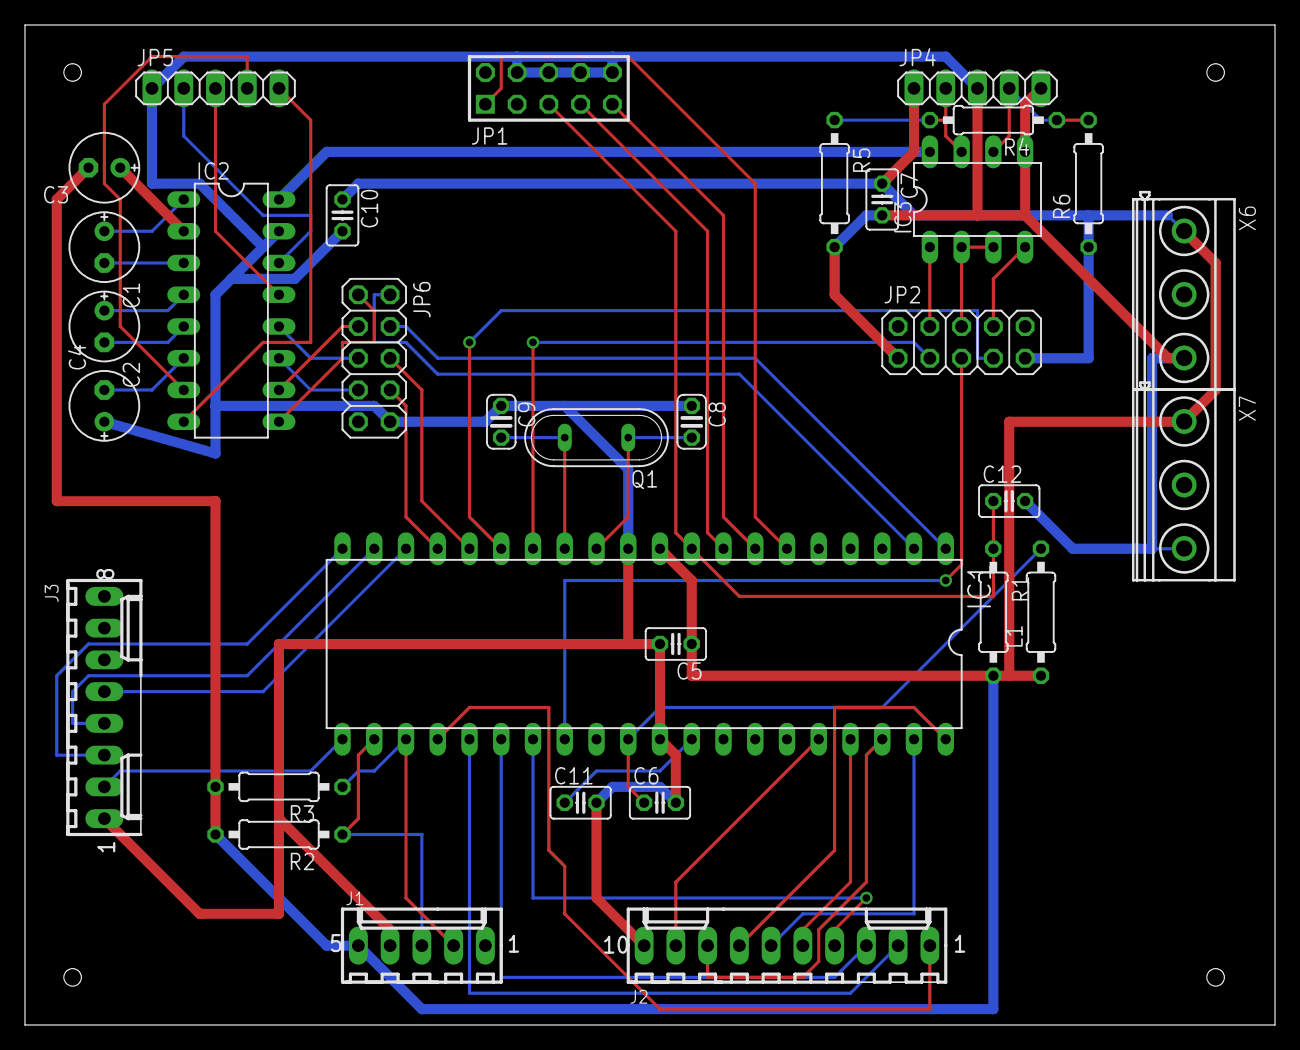
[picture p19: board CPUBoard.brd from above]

Board: 2 copper layers, 100.0 x 80.0 mm, 33 parts (0 on the bottom side), 52 nets.

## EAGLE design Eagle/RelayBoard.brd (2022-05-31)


Board: 2 copper layers, 100.0 x 80.0 mm, 13 parts (0 on the bottom side), 33 nets.

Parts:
C1: 100nF; C025-025X050
IC1: ULN2003AN; DIL16
K1, K2, K3: 4052; F4052
X1, X2: MKDSN1,5/6-5,08
X3: Con1; KK-156-9
X5: MKDSN1,5/4-5,08
X6: MKDSN1,5/2-5,08
X7: Con2; KK-156-5
X8, X9: KK-156-3

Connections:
0V: C1.2, IC1.8, X3.9, X7.4, X7.5, X8.1, X9.1
+5V: X3.1, X7.3
+12V: C1.1, IC1.9, K1.1, K2.1, K3.1, X7.1, X7.2
unnamed: K3.P1, X6.1
unnamed: K3.P2, X6.2
unnamed: K3.S1, X5.1, X5.2
unnamed: IC1.16, K3.2
unnamed: K3.S2, X5.3, X5.4
unnamed: K2.P1, X2.1
unnamed: K2.S1, X2.2
unnamed: K2.O1, X2.3
unnamed: K2.P2, X2.4
unnamed: K2.S2, X2.5
unnamed: K2.O2, X2.6
unnamed: K1.P1, X1.1
unnamed: K1.S1, X1.2
unnamed: K1.O1, X1.3
unnamed: K1.P2, X1.4
unnamed: K1.S2, X1.5
unnamed: K1.O2, X1.6
unnamed: IC1.1, X3.2
unnamed: IC1.2, X3.3
unnamed: IC1.3, X3.4
unnamed: IC1.4, X3.5
unnamed: IC1.5, X3.6
unnamed: IC1.6, X3.7
unnamed: IC1.7, X3.8
unnamed: IC1.15, K2.2
unnamed: IC1.14, K1.2
unnamed: IC1.11, X8.3
unnamed: IC1.10, X8.2
unnamed: IC1.13, X9.3
unnamed: IC1.12, X9.2

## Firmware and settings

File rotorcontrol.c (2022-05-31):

/*
 * File   : rotorcontrol.c
 *
 * Copyright:      Hermann-Josef Mathes  mailto: dc2ip@darc.de
 * Author:         Hermann-Josef Mathes
 * Remarks:
 * Known problems: development status
 * Version:        Version v1r0
 * Description:    Program which performs the rotator control.
 *

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
   Falls nicht, schreiben Sie an die Free Software Foundation,
   Inc., 59 Temple Place, Suite 330, Boston, MA 02111-1307, USA.

 *
 */

#include <stdint.h>
#include <stdlib.h>
#include <string.h>

/** @file rotorcontrol.c
  * main() of the rotator control program.
  * @author H.-J. Mathes <dc2ip@darc.de>
  */

#include <avr/io.h>
#include <avr/interrupt.h>
#include <avr/pgmspace.h>
#include <avr/eeprom.h>
#include <util/delay.h>

#include <i2cmaster.h>   // P.Fleury's lib

#include "global.h"

#include <uart.h>        // P.Fleury's lib

#include "vector.h"
#include "i2cdisplay.h"

#define UART_BAUD_RATE 9600

// Fuses and programming:
//
// Factory settings:
//  Device signature = 0x1e9502
//  hfuse = 0x99
//  lfuse = 0xE1
//
// avrdude -p atmega32 -P usb -c usbasp -y -Y 0
//
// avrdude -p atmega32 -P /dev/parport1 -c stk200 -y -U flash:w:rotorcontrol.hex
//
// avrdude -p atmega32 -P usb -c usbasp -y -U flash:w:rotorcontrol.hex
//
// avrdude -p atmega32 -P usb -c usbasp -y -U lfuse:r:-:i -U hfuse:r:-:i
// avrdude -p atmega32 -P usb -c usbasp -y -U hfuse:w:0xC1:m
//  - JTAG disabled
//  - CKOPT enabled
//  - EESAVE enabled
// avrdude -p atmega32 -P usb -c usbasp -y -U lfuse:w:0xEE:m
//  - external crystal (CKSEL3..1 = 111)
//
// avrdude -p atmega32 -P usb -c usbasp -y -U eeprom:w:rotorcontrol.eep
// avrdude -p atmega32 -P usb -c usbasp -y -U eeprom:r:-:i
//
// //avrdude -p atmega32 -P usb -c usbasp
//
// avrdude -p atmega32 -P usb -c usbasp -y -U flash:w:avrledtest.hex
// avrdude -p atmega32 -P usb -c usbasp -y -U flash:w:displaytest.hex
//

// local prototypes

static void delay_sec(uint8_t);

// --------------------------------------------------------------------------

// configuration storage in EEPROM

uint16_t gLimitAngle EEMEM = LIMIT_ANGLE;

//i_vector_t gEE_MAG_min EEMEM = { -474, -257, -257 };
//i_vector_t gEE_MAG_max EEMEM = {   36,  238,  238 };
vector_t gEE_MAG_min EEMEM = { -474, -257, -257 };
vector_t gEE_MAG_max EEMEM = {   36,  238,  238 };

// --------------------------------------------------------------------------

// ISR for timer/counter 0 overflow: called every 10 ms
// - load counter with initial constant
// - call button check routine

ISR(TIMER0_OVF_vect) {

  TCNT0 = CNT0_PRESET;

  // call button check routine
  CheckKeys();

  // rotator command interface
  if ( gRotatorBusyCounter )
    gRotatorBusyCounter--;
  else
    RotatorExec();

  // execute 'Preset' program
  PresetExec();

  // will switchoff 'Preset' display after some time
  if ( gPresetDisplayCounter > 0 )
    gPresetDisplayCounter--;
}

// --------------------------------------------------------------------------

static void InitHardware(void) {

  delay_sec( 1 );

  // timer 0 initialisation
  TCNT0 = CNT0_PRESET;
  TCCR0 = (1<<CS02)|(1<<CS00);  // CK/1024 -> 1 tick each .128 msec

  // enable timer overflow interrupt
  TIMSK |= (1<<TOIE0);

  uint8_t mask;

  // relay port initialisation, all relays off
  mask = RELAY_POWER | RELAY_CW | RELAY_CCW | RELAY_STOP;

  RELAY_PORT &= ~mask;
  RELAY_DDR |= mask;

  // LED port initialisation, all LEDs off, RS485 RX enable
  mask = LED_LEFT | LED_RIGHT | LED_CALIBRATE | LED_OVERLOAD;

  LED_PORT &= ~mask;
  LED_DDR |= mask;

  RS485EnableRx();
  RS485_DDR |= RS485_TX_ENABLE;

  // Buttons port initialisation, turn pull-ups on
  mask = BUTTON_PRESET_CCW | BUTTON_CCW | BUTTON_STOP | BUTTON_CW |
  BUTTON_PRESET_CW;

  BUTTON_PORT |= mask;
  BUTTON_DDR &= ~mask;

  // initialize USART0 (receiving NMEA messages via RS485 from ACC/MAG sensor)
  uart_init( UART_BAUD_SELECT(UART_BAUD_RATE,F_CPU) );

  // initialize USART1, for command/status exchange with HAM op (& debug)

  // enable interrupts globally
  sei();

  // init I2C interface
  i2c_init();

  I2CDisplayBlank();
  I2CDisplayOn();
}

// --------------------------------------------------------------------------

static const uint8_t cStartMessage[] PROGMEM =
         { 0x7a, 0x65, 0x6b, 0x12, 0x4f, 0x00 }; // "dC2" "IP "
//         { 0x01, 0x02, 0x04, 0x08, 0x10, 0x20 };  // test pattern

static const uint8_t cPauseMessage[] PROGMEM =
         { 0x08, 0x08, 0x08, 0x08, 0x08, 0x08 }; // "---" "---"

static void StartMessage(uint8_t n_sec) {

  I2CDisplayWrite_p( sizeof(cStartMessage), cStartMessage );
  I2CDisplayOn();

  delay_sec( n_sec );

  I2CDisplayWrite_p( sizeof(cPauseMessage), cPauseMessage );

  delay_sec( 1 );

  I2CDisplayBlank();
}

// --------------------------------------------------------------------------

int main(void) {

  // initialize the hardware ...
  InitHardware();

  // reset the message decoding engine
  CompassMessageInit();

  // initialize the compass calculator
  CompassInit();

  // display the start message, and leave it for # seconds on
  StartMessage(2);

  unsigned int uart_data;

  while ( 1 ) {

   // --- handle serial messages (from ACC/MAG sensor)

   if ( (uart_data = uart_getc()) != UART_NO_DATA ) {

     CompassMessageReceive( uart_data );
   }

   // --- handle serial messages from RS232 interface

     // ...

   // --- update of heading display

    UpdateDisplay();

   // --- 5 button user interface to rotator control

    // --- checks for BUTTON CCW ---

    if ( (gKeyState & BUTTON_CCW) && !(gKeyState & BUTTON_STOP)
                                   && !IsRotatorBusy() ) {

      SetCommand( kTurnCCW );
    }

    // was BUTTON CCW released ?

    if ( (GetLastCommand() == kTurnCCW) && !(gKeyState & BUTTON_CCW) ) {

      SetCommand( kStop );
    }

    // --- checks for BUTTON CW ---

    if ( (gKeyState & BUTTON_CW) && !(gKeyState & BUTTON_STOP)
                                    && !IsRotatorBusy() ) {

      SetCommand( kTurnCW );
    }

    // was BUTTON CW released ?

    if ( (GetLastCommand() == kTurnCW) && !(gKeyState & BUTTON_CW) ) {

      SetCommand( kStop );
    }

    // --- checks for BUTTON STOP ---

    if ( gKeyState & BUTTON_STOP ) {

      SetCommand( kFastStop );
    }

    // --- checks for BUTTON PRESET CCW ---

    if ( gKeyState & BUTTON_PRESET_CCW ) {

      SetPresetCommand( kPresetCCW );
    }

    if ( (gPresetCommand == kPresetCCW) && !(gKeyState & BUTTON_PRESET_CCW) ) {

      SetPresetCommand( kPresetStop );
    }

    // --- checks BUTTON PRESET CW ---

    if ( gKeyState & BUTTON_PRESET_CW ) {

      SetPresetCommand( kPresetCW );
    }

    if ( (gPresetCommand == kPresetCW) && !(gKeyState & BUTTON_PRESET_CW) ) {

      SetPresetCommand( kPresetStop );
    }

  } // while ( 1 ) ...

  return 0;
}

// --------------------------------------------------------------------------

/** Active delay for a given number of seconds (up to 255). */
static void delay_sec(uint8_t n_sec) {

  while ( n_sec ) {
    // inline in util/delay.h
    for ( int m=0; m<100; m++ )
      _delay_ms( 10.0 );
    n_sec--;
  }
}

// --------------------------------------------------------------------------
// --------------------------------------------------------------------------

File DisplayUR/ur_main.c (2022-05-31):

/*----------------------------------------------------------------------------
 Copyright:      Radig Ulrich  mailto: mail@ulrichradig.de
 Author:         Radig Ulrich
 Remarks:
 known Problems: none
 Version:        11.01.2009
 Description:    Power Supply LED Display

 Dieses Programm ist freie Software. Sie können es unter den Bedingungen der
 GNU General Public License, wie von der Free Software Foundation veröffentlicht,
 weitergeben und/oder modifizieren, entweder gemäß Version 2 der Lizenz oder
 (nach Ihrer Option) jeder späteren Version.

 Die Veröffentlichung dieses Programms erfolgt in der Hoffnung,
 daß es Ihnen von Nutzen sein wird, aber OHNE IRGENDEINE GARANTIE,
 sogar ohne die implizite Garantie der MARKTREIFE oder der VERWENDBARKEIT
 FÜR EINEN BESTIMMTEN ZWECK. Details finden Sie in der GNU General Public License.

 Sie sollten eine Kopie der GNU General Public License zusammen mit diesem
 Programm erhalten haben.
 Falls nicht, schreiben Sie an die Free Software Foundation,
 Inc., 59 Temple Place, Suite 330, Boston, MA 02111-1307, USA.
----------------------------------------------------------------------------*/

#include <avr/interrupt.h>
#include <avr/io.h>

#include "multiplex.h"
#include "adc.h"

//---------------------------------------------------------------------------
int main (void)
{

	DDRD |= (1<<PD0)|(1<<PD1)|(1<<PD2)|(1<<PD3)|(1<<PD4)|(1<<PD5)|(1<<PD6);
	DDRB |= (1<<PB0)|(1<<PB1)|(1<<PB2)|(1<<PB3)|(1<<PB4)|(1<<PB5);

	adc_init();

	sei();

	MultiplexInit();

	while(1)
	{
		if (adc_count > 400)
		{
			//ADC_OFF();
			gMultiplexDisplay1 = (display_value_1 / adc_count);
			gMultiplexDisplay2 = (display_value_2 / adc_count);
			adc_count = 0;
			display_value_1 = 0;
			display_value_2 = 0;
			//ADC_ON();
		}
	}
}

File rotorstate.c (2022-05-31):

/*
 * File   : rotorstate.c
 *
 * Copyright:      Hermann-Josef Mathes  mailto: dc2ip@darc.de
 * Author:         Hermann-Josef Mathes
 * Remarks:
 * Known problems: development status
 * Version:        Version v1r0
 * Description:    State machine for the rotator control program.
 *

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
 *
 */

#include <stdint.h>
#include <stdlib.h>

/** @file rotorstate.c
  * State machine for the rotator control program.
  * @author H.-J. Mathes <dc2ip@darc.de>
  */

#include <avr/io.h>
#include <avr/interrupt.h>
#include <avr/pgmspace.h>
#include <util/delay.h>

#include <i2cmaster.h>   // P.Fleury's lib

#include "global.h"

#include <uart.h>

#include "i2cdisplay.h"
#include "num2uart.h"

volatile uint8_t gRotatorBusy = 0;
volatile uint8_t gRotatorCommand = kNone;
volatile uint8_t gRotatorState = kIdle;
volatile uint8_t gRotatorBusyCounter = 0;

#define SetBusy(_busy_) { gRotatorBusy = _busy_; }

volatile static int16_t gCurrentHeading = 0;
volatile static int16_t gPresetHeading = 0;

#define PRESET_COUNTER_MAX           32
#define PRESET_COUNTER_MIN           4

volatile uint8_t gPresetCommand = kPresetNone;
static uint8_t gPresetCounterStart = PRESET_COUNTER_MAX;
volatile uint8_t gPresetCounter = 0;

/* local prototypes */
static uint8_t GetDirection(uint16_t cur_heading,uint16_t nom_heading);

// --------------------------------------------------------------------------

/** The state machine of the rotor control engine ...
 *
 * This is the transition diagram after the command kRotateCW has been issued:
 *
 * kRotateCW -> kIdle
 *                |
 *                | ==> PowerOn()
 *               \/
 *              kReleaseBrake
 *                |
 *       kStop -> | -------- >>> -------+
 *                | ==> ReleaseBrake()  |
 *                |                     |
 *               \/                     |
 *              kRotorRampup            |
 *                |                     |
 *       kStop -> | -------- >>> -------|--+
 *                | ==> RotateCW()      |  |
 *                |                     |  |
 *               \/                     |  |
 *              kTurningCW              |  |
 *                |                     |  |
 *                * <-------------------+  |
 *       kStop -> |                        |
 *                | ==> RotorOff()         |
 *                |                        |
 *               \/                        |
 *              kLockBrake                 |
 *                |                        |
 *                * <----------------------+
 *                |
 *                | ==> LockBrake()
 *                |
 *               \/
 *              kRotorRampdown
 *                |
 *                | ==> PowerOff()
 *                |
 *               \/
 *              kIdle
 *
 * It will be handled in a similar way for the command kRotateCCW.
 *
 * As the trasitions will take some time, it is not unlikely, that the kStop
 * event is issued before the state kTurningCW is reached. In that case the
 * rotor relays etc. must be switched off in a proper order.
 */
void RotatorExec(void) {

  switch ( gRotatorCommand ) {

    case kStop:

	 SetBusy(1);

	 switch ( gRotatorState ) {

	   case kReleaseBrake: // ???
	   case kTurningCW:
	   case kTurningCCW:
	        RotatorOff();
		gRotatorBusyCounter = 5;
		gRotatorState = kLockBrake;
	        break;

	   case kRotorRampup: // ???
	   case kLockBrake:
	        BrakeLock();
		gRotatorBusyCounter = 5;
		gRotatorState = kRotorRampdown;
	        break;

	   case kRotorRampdown:
		PowerOff();
	        gRotatorState = kIdle;
		gRotatorBusyCounter = 10;
	        break;

	   case kIdle:
		gRotatorCommand = kNone;
		SetBusy(0);
	        break;
	 }

         break;

    case kTurnCW:

	 SetBusy(1);

	 switch ( gRotatorState ) {

	   case kIdle:
	        PowerOn();
		gRotatorState = kReleaseBrake;
		gRotatorBusyCounter = 10;
		break;

	   case kReleaseBrake:
	        BrakeRelease();
		gRotatorState = kRotorRampup;
		gRotatorBusyCounter = 5;
		break;

	   case kRotorRampup:
		gRotatorState = kTurningCW;
         	RotatorCW();
		gRotatorBusyCounter = 5;
		break;

	   case kTurningCW:
		gRotatorState = kTurningCW;
	        gRotatorCommand = kNone;
		break;
	 }

         break;

    case kTurnCCW:

	 SetBusy(1);

	 switch ( gRotatorState ) {

	   case kIdle:
	        PowerOn();
		gRotatorState = kReleaseBrake;
		gRotatorBusyCounter = 10;
		break;

	   case kReleaseBrake:
	        BrakeRelease();
		gRotatorState = kRotorRampup;
		gRotatorBusyCounter = 5;
		break;

	   case kRotorRampup:
		gRotatorState = kTurningCCW;
         	RotatorCCW();
		gRotatorBusyCounter = 5;
		break;

	   case kTurningCCW:
		gRotatorState = kTurningCCW;
	        gRotatorCommand = kNone;
		break;
	 }

         break;

    case kFastStop:
         RotatorOff();
         BrakeLock();
	 PowerOff();

	 // reset state machine and command variable
	 gRotatorState = kIdle;
	 gRotatorCommand = kNone;

         // both PRESET LEDs off
         LED_PORT &= ~(LED_LEFT | LED_RIGHT);

	 SetBusy(0);

         // clear preset data
         gPresetHeading = gCurrentHeading;
	 gPresetCounter = 0;
	 gPresetCommand = kPresetNone;
         break;

    default:
         break;
  }
}

// --------------------------------------------------------------------------

static uint8_t gLastCommand = kNone;

void SetCommand(uint8_t cmd) {

  gLastCommand = gRotatorCommand;
  gRotatorCommand = cmd;
}

// --------------------------------------------------------------------------

uint8_t GetLastCommand(void) {

  return gLastCommand;
}

// --------------------------------------------------------------------------

volatile uint16_t gPresetDisplayCounter = 0;

static uint16_t gCurrentHeadingOld = 999;
static uint16_t gPresetHeadingOld = 999;

// called by main()
void UpdateDisplay(void) {

  static uint8_t ret = 0;

  if ( gCurrentHeadingOld != gCurrentHeading ) {

    gCurrentHeadingOld = gCurrentHeading;

    if ( ret ) {
      i2c_init();

      _delay_ms(10.0);
    }

    ret = I2CDisplayWriteLData( gCurrentHeading );

    _delay_ms(1.0);
  }

  if ( gPresetHeadingOld != gPresetHeading ) {

    gPresetHeadingOld = gPresetHeading;

    if ( ret ) {
      i2c_init();

      _delay_ms(10.0);
    }

    ret = I2CDisplayWriteRData( gPresetHeading );

    _delay_ms(1.0);

    // 'PRESET' display should vanish after 5 sec if both are equal
    if ( gCurrentHeading == gPresetHeading ) {

      // atomic set uint16_t type variable
      cli();
       gPresetDisplayCounter = 500;
      sei();
    }
  }

  // 'PRESET' display should vanish after 5 sec if both are equal
  if ( gCurrentHeading == gPresetHeading ) {

    if ( gPresetDisplayCounter == 0 )
      //I2CDisplayWriteR( 3, (uint8_t*)"\000\000\000" );  // blank display
      I2CDisplayWriteR( 3, (uint8_t*)"\010\010\010" );    // "---"
  }
}

// --------------------------------------------------------------------------
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

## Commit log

2011-07-19 - from U.Radig imported sources of PowerSupply - drawings and schemes go to DisplayUR/Doc
    [Power_Supply.brd, Power_Supply.sch]
2011-10-04 - simple I2C test program for LSM303DLH (w.i.p)
2011-10-24 - more tests on hardware, some fixes
    [LSM303DLH.c, lsm303test.c]
2011-10-26 - reading ACC via LSM303DLH library function - added get8key4.c to read button inputs (P.Dannegger) + definition file global.h - lsm303read.c: read values and send via RS-232 - added num2int.* to pro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
2011-10-27 - lsm303read.c: - code slightly rearranged, to be tested - NMEA 0183 compatible output foreseen (can be switched) - num2uart.c: const arrays now static
2011-10-27 - some corrections to strings - strcat_p() fixed
    [lsm303read.c]
2011-11-22 - compass2.cc: read sensor data via RS232 and calc. heading; -> probably names and organization will change...
2011-11-29 - main.c -> ur_main.c, Makefile modified - UR's source files slightly beautified - started with i2cdisplay ... not yet compiling
2011-12-02 - i2cdisplay: first test code, just displaying something...
2011-12-03 - for i2cdisplay 'products'
2011-12-05 - testing board with i2cdisplay (2.12.) --> OK -> decimal points must be wired, too & disconnected from static level - new Makefile, now generated by mfile.tcl -> '-lm' is really needed (code size!) 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
2011-12-27 - switched interrupt routine to read from segment buffer - twitest.c: I2C master for testing the display + Makefile.twitest ... (different clock frequencies)
2011-12-27 - fixed a few (partly my own) bugs in i2cslave.c - basic protocol defined, most parts unimplemented
    [i2cdisplay.c, twitest.c]
2011-12-27 - documented current status in master CHANGES file
2011-12-29 - button control for LEFT/RIGHT added - timer controlled button query integrated -> not yet tested !
2011-12-29 - defs. for BRAKE exchanged
2012-01-03 - twitest.c: - test of other command types implemented - i2cdisplay.*: - most of other command types implemented, too -> test successful! - completed protocol documentation - fix of command types (du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
    [i2cdisplay.c, twitest.c]
2012-01-25 - definition for rotor power relay
2012-01-26 - changed pin assignment, circuit diagram gets nicer ;)
2012-01-26 - circuit for relay board added
    [RelayBoard1.sch]
2012-03-23 - present working state
    [RelayBoard.brd, RelayBoard1.sch]
2012-03-30 - more boards added
    [ButtonBoard.brd, ButtonBoard.sch, CPUBoard.sch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]
2012-03-30 - more boards (circuit diagrams) added
2012-04-04 - correction to RelayBoard2 - added schematic for PowerSupply (no board so far)
    [PowerSupply.sch, RelayBoard2.brd, RelayBoard2.sch]
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2012-04-10 - some modifications, corrections, ...
    [ButtonBoard.brd, ButtonBoard.sch, RelayBoard1.brd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]
2012-04-11 - more stuff added
    [CPUBoard.sch]
2012-04-11 - overview 40 pin variants
2012-04-18 - CPUBoard near final ...
    [CPUBoard.sch]
2012-04-18 - changed global.h according to recent CPUboard schematic - initialisation code for LEDs and BUTTONs added
2012-04-19 - CPUBoard: jumper block for serial interface, MAX232 | USB
    [CPUBoard.sch]
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2012-05-04 - CPUBoard with some corrections - two-sided board routed (demo), component placement
    [CPUBoard.brd, CPUBoard.sch]
2012-05-06 - corrections for CPUBoard: - RS-485 need termination resistors etc. - connectors are wrong, use 22-?-05 tec. from con-molex -> connectors on other boards must be replaced, too!
    [CPUBoard.brd, CPUBoard.sch]
2012-05-07 - corrections for RelayBoard1: - using right connectors from library con-molex - single sided routing - corrections for ButtonBoard: - using right connector from library con-molex - using right switc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
    [ButtonBoard.brd, ButtonBoard.sch, CPUBoard.brd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]
2012-05-08 - CPUBoard: - another pin-header added for RS-485 UART - correct termination for RS-485 A/B lines - PowerSupply: terminals added - eagle_clean.sh: remove backup files of Eagle
    [CPUBoard.brd, CPUBoard.sch, PowerSupply.sch]
2012-05-09 - small corrections
    [PowerSupply.sch]
2012-05-09 - ATmega32 put finally on board -> fuse programming (see rotorcontrol.c) -> test with avrledtest (OK)
2012-05-10 - CPUBoard: fix connections to display, somehow mirrored
    [CPUBoard.brd, CPUBoard.sch]
2012-05-10 - wiring from/to MAX232 changed slightly
    [CPUBoard.brd, CPUBoard.sch]
2012-05-10 - another fix for the TWI pins, hopefully the last one!
    [CPUBoard.brd, CPUBoard.sch]
2012-05-10 - swapped connections to relay board1
    [CPUBoard.brd, CPUBoard.sch]
2012-05-11 - directory for test programs: Test - displaytest.c etc. moved here - blrtest.c: test program for buttons, LEDs and relays
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2012-05-11 - started with AntennaBoard
    [AntennaBoard.sch]
2012-05-12 - swapped LED_L and LED_R in schematic - solder bridge between two buttons found and fixed
    [CPUBoard.brd, CPUBoard.sch]
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2012-05-12 - fixed double enums
    [global.h]
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2012-05-13 - cabling of RelayBoard1 partly changed - some pin-swaps to ButtonBoard -> blrtest.c finally works as expected
    [CPUBoard.brd, CPUBoard.sch, RelayBoard1.brd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]
2012-05-14 - meaning of relay pins swapped
    [global.h]
2012-05-15 - PowerSupply: schematic continued, proposal for board layout
    [PowerSupply.brd, PowerSupply.sch]
2012-05-16 - multiplex.c: 7-segment to port mapping documented - i2cdisplay.h -> i2cdisplaydefs.h
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2012-05-16 - removed lcd.h lcd.c device.h, compass.c kept as example code
2012-05-17 - logic slightly changed, no bouncing between STOP and L/R buttons
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2012-05-18 - activated UART stuff and decoding routines (untested) - pass mcu to avr-size command
2012-05-20 - GPL V3 short license text added
    [i2cdisplay.c, rotorcontrol.c, rotorstate.c]
2012-05-20 - copyright stuff added (GNU GPL v3) - 'LED_DEBUG' switched off
2012-05-21 - copyright stuff added (GNU GPL v3) - blrtest.c adopted to changed button definitions - started with this combined README/CHANGES files
2012-05-22 - modifications to run on ATtiny2313: - requires i2cmaster.S instead of twimaster.c + use USI pins of ATtiny2313 - i2cmaster.c -> twimaster.c
2012-05-24 - AntennaBoard: finalized (?) and first board layout
    [AntennaBoard.brd, AntennaBoard.sch]
2012-05-24 - flag 'LED_DEBUG' never used, removed - flag 'NMEA_FORMAT' now steered from Makefile
2012-05-24 - working on lsm303read.c: - use of global.h for standard program, too - macros to steer MAX485 chip - timer for periodic sensor readout
2012-05-25 - IPS-Header added to AntennaBoard, U.Radig layout
    [AntennaBoard.brd, AntennaBoard.sch]
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2012-05-28 - changed clock frequency to 2 MHz (otherwise UART inprecise) -> constants for 100ms re-calculated - define SENSOR_READOUT_PERIOD: 200ms
2012-05-28 - current fuse settings (2 MHz internal OSC) documented
2012-05-28 - RS485 stuff (Rx/Tx enable) for our board added
2012-06-03 - heading calculation now included + linking with scanf-library for floating point !? + or using atoi() based string parsing (saves 2.5k) + vector.c and num2uart.c included into Makefile - heading wr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
2012-06-04 - heading calculation fixed, first mounting of mockup
    [compass.c, global.h, rotorstate.c]
2012-06-04 - first version with 'preset' -> with some problems ...
    [compass.c, global.h, rotorcontrol.c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]
2012-06-04 - slightly improved, still problems...
    [compass.c, global.h, rotorcontrol.c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]
2012-06-07 - actions for 'preset' functionality disabled + catch position always moving
    - messages to UART sometimes corrupt, fixed
    -> UART_TX_BUFFER_SIZE, UART_RX_BUFFER_SIZE in Makefile
    + different sizes (RX buffer large)
    - read constants from EEPROM failed with int16_t -> float OK
    [compass.c, global.h, rotorcontrol.c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]
2012-06-07 - additional (commented out) definitions for RS485 pin/port, this is compatible with chip45boot2 boot loader
2012-06-07 - additional (commented out) definitions for RS485 pin/port, this is compatible with chip45boot2 boot loader - modified Makefile to do right linking when bootloader is used + hints for new fuse bit s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
2012-06-11 - analyzedat.cc: - MAG-sensor calibration off by default - optional creation of ROOT histograms
2013-04-05 - AntennaBoard: ERC errors fixed, worked on board and DRC - PowerSupply: ERC & DRC errors fixed
    [AntennaBoard.brd, AntennaBoard.sch, PowerSupply.brd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]
2013-09-24 - fixed some error, re-routing done
    [PowerSupply.brd, PowerSupply.sch]
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2022-05-31 pre-commit run --all-files
    [AntennaBoard.brd, AntennaBoard.sch, ButtonBoard.brd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]

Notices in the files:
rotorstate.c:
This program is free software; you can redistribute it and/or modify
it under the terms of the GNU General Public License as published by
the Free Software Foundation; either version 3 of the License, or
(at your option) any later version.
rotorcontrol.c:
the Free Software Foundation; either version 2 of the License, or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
